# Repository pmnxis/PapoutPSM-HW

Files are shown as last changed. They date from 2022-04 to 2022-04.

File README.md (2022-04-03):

# PapoutPSM-HW

| 3D Model | Real Image |
| --- | --- |
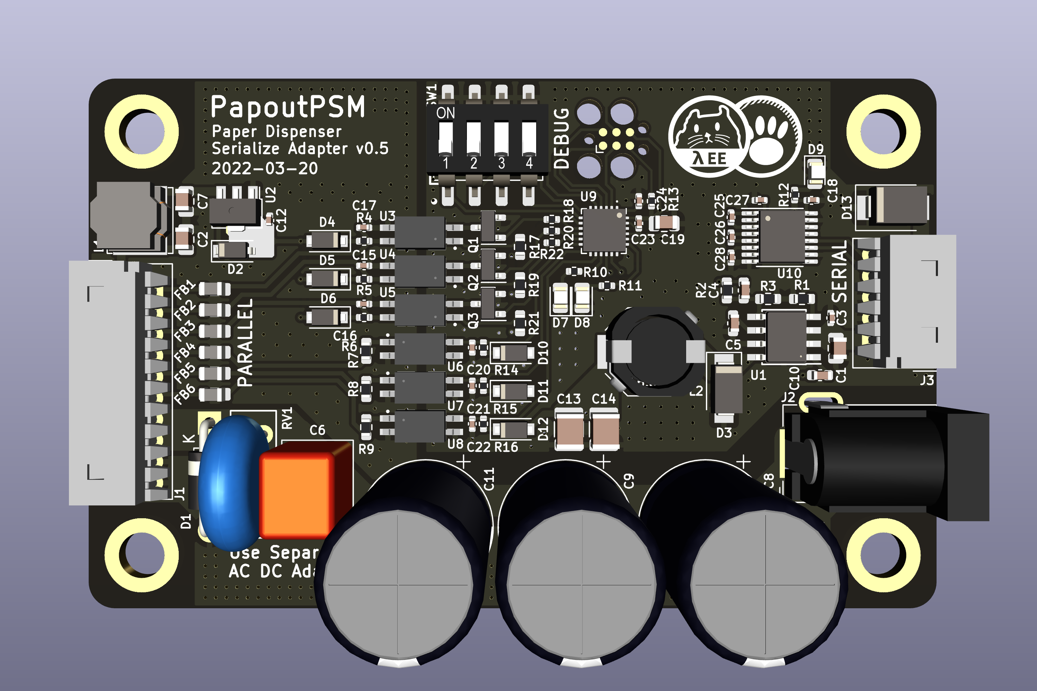
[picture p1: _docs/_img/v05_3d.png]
PCB 3D MODEL
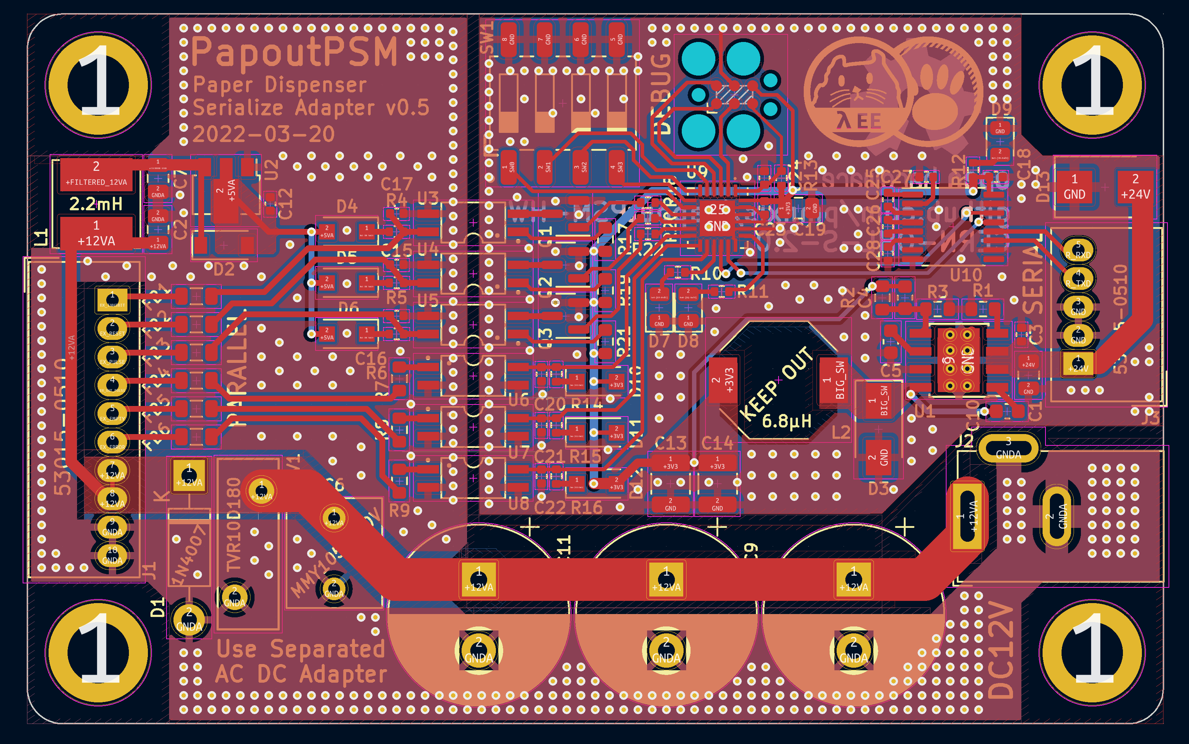
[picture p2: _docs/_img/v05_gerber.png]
GerberImage
|  |  |

Parallel to Serial Adapter for Korean Paper Dispenser Machine.
Some wellknown korean paper dispenser have two type of device.
Serial model communicate to host with RS232.

## PCB Specification
- DRC/Fabrication Clearance : JLCPCB Standard 2 Layer Spec.
- PCB : 2Layer FR4 ; 1.6T , Considerd on black colour.
- Size : 80mm * 50mm

## Power Connection
### 12V Usage (Normal)
- Connect Secondary Power Source (ACDC Adapter) 12VDC (5A) to barral jack.
- Use default varistor (RV1). Default is `10Ø 18V`.

### 24V Usage
- Connect Secondary Power Source (ACDC Adapter) 24VDC (3A) to barral jack.
- Use custom varistor (RV1). Must be higher or eqeual with `30V`.

### Programming
- MSP430FR2433 with CCStudio.
- or with Rust? https://github.com/rust-embedded/msp430-quickstart
- Emulating dispenser machine should count exhaust or some configuration on non violent storage. MSP43FR have internal FeRAM. Thus ensure high durability on many write operation.

### Related Project 
https://github.com/pmnxis/papout-psm-rs

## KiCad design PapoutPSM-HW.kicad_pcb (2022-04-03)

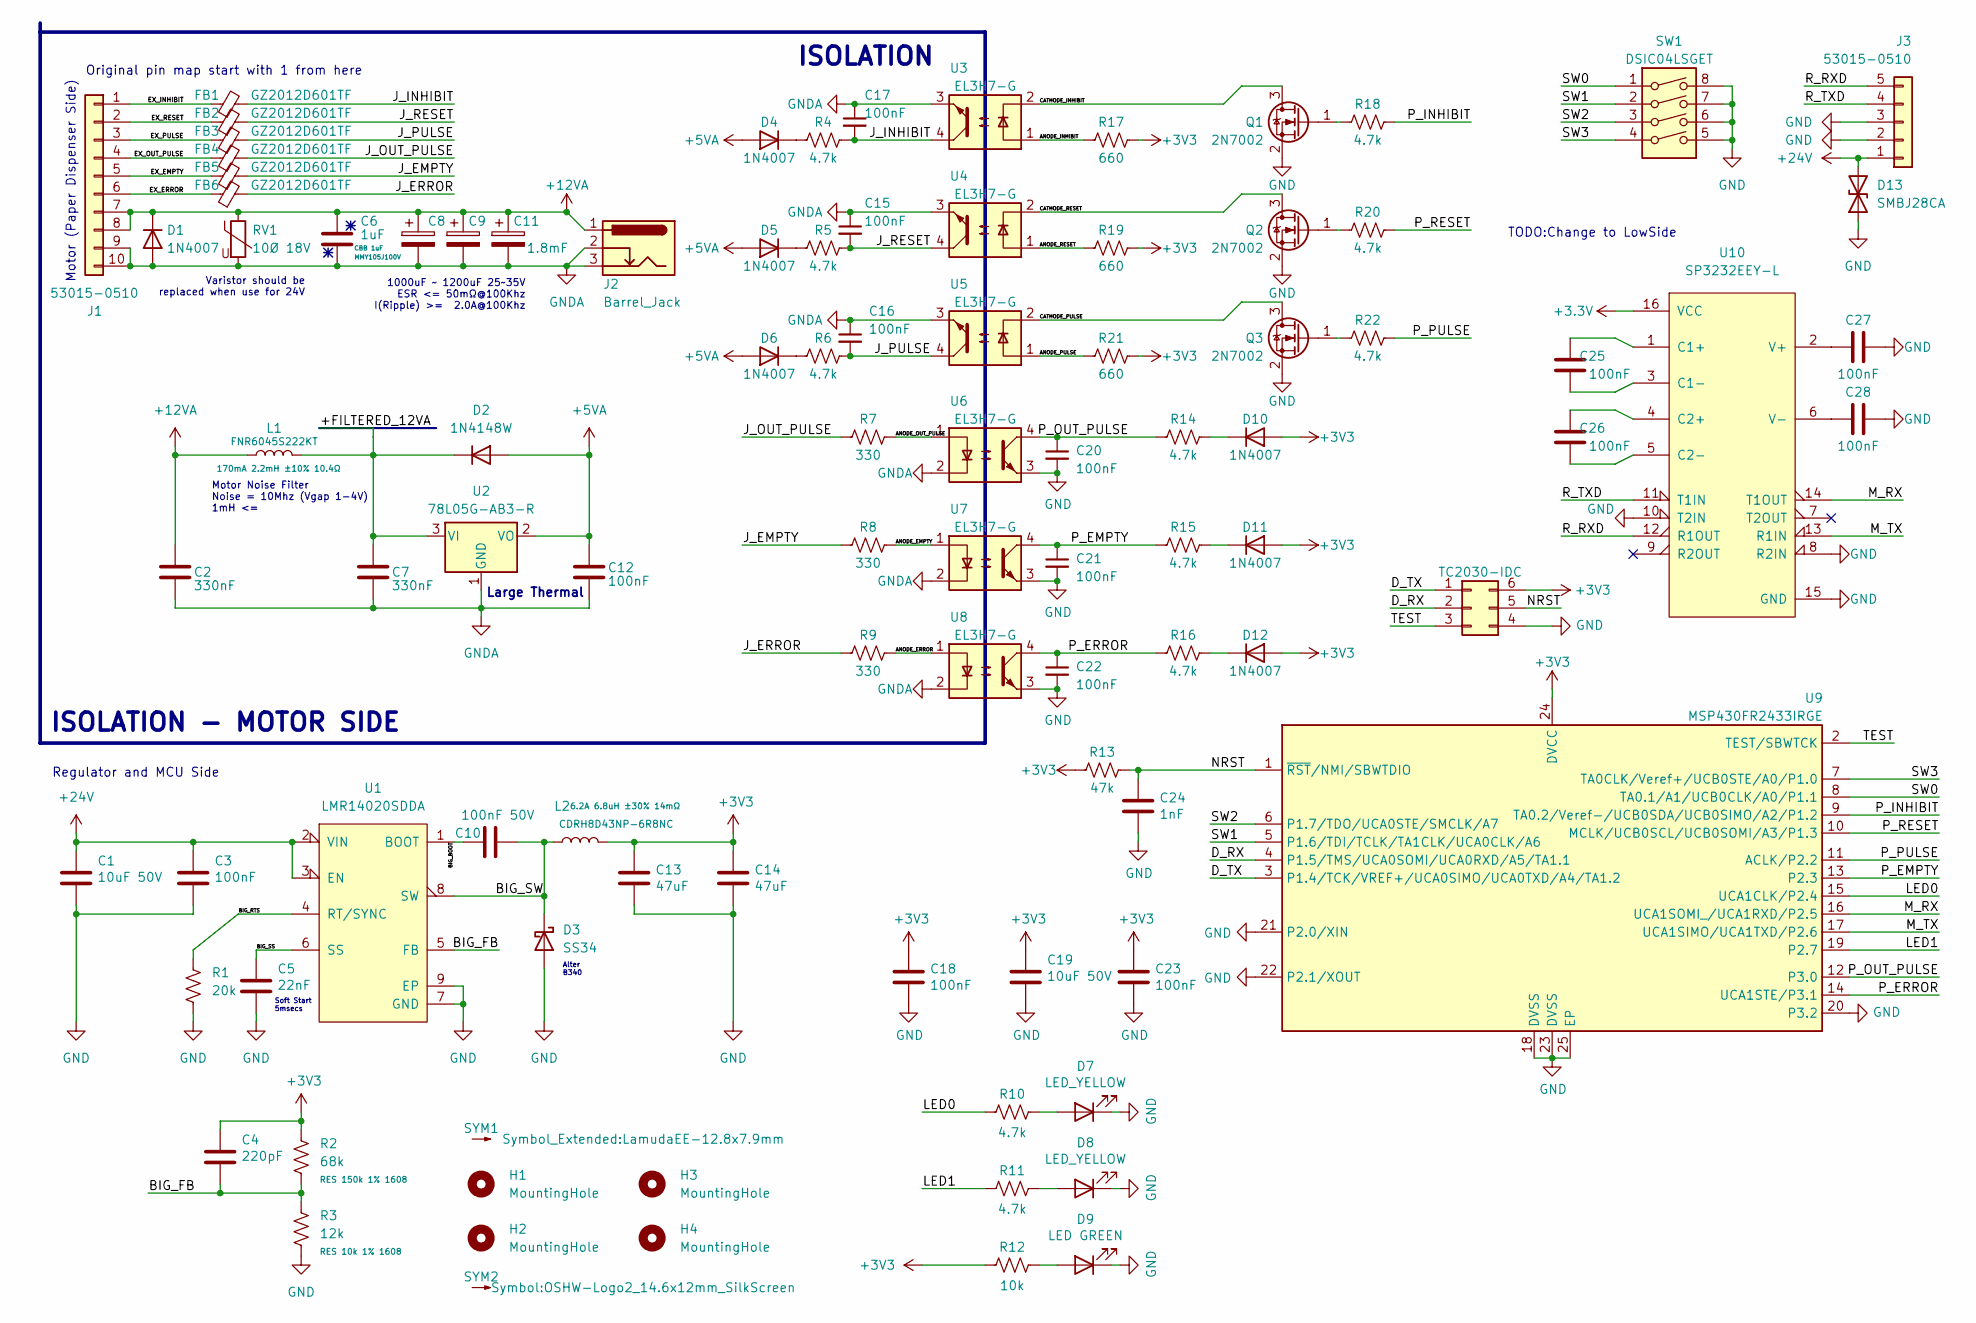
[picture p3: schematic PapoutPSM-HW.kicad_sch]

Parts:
C1, C19: 10uF 50V; C_0805_2012Metric; MFR.Part# GRM21BR61H106KE43L; LCSC Part C440198
C2, C7: 330nF; C_0805_2012Metric; MFR.Part# 0805B334K500NT; LCSC Part C1740
C3, C12, C15, C16, C17, C18, C20, C21, C22, C23, C25, C26, C27, C28: 100nF; C_0402_1005Metric; MFR.Part# CL05B104KB54PNC; LCSC Part C307331
C4: 220pF; C_0603_1608Metric; MFR.Part# CL10C331JB8NNNC; LCSC Part C1664
C5: 22nF; C_0603_1608Metric; MFR.Part# CL10B223KB8NNNC; LCSC Part C21122
C6: 1uF; C_Rect_L7.5mm_W6.5mm_P5.00mm; MFR.Part# MMY105J100V
C8, C9, C11: 1.8mF; CP_Radial_D12.5mm_P5.00mm; MFR.Part# LKML2501V182MF; LCSC Part C442894
C10: 100nF 50V; C_0603_1608Metric; MFR.Part# CC0603KRX7R9BB104; LCSC Part C14663
C13, C14: 47uF; C_1210_3225Metric; MFR.Part# GRM32ER61C476KE15L; LCSC Part C77101
C24: 1nF; C_0402_1005Metric; MFR.Part# 0402B102K500NT; LCSC Part C1523
D1: 1N4007; D_DO-41_SOD81_P10.16mm_Horizontal
D2: 1N4148W; D_SOD-123
D3: SS34; D_SMA; MFR.Part# SS34; LCSC Part C8678
D4, D5, D6, D10, D11, D12: 1N4007; D_SOD-123F
D7, D8: LED_YELLOW; LED_0805_2012Metric; MFR.Part# KT-0805Y; LCSC Part C2296
D9: LED GREEN; LED_0805_2012Metric; MFR.Part# KT-0805G; LCSC Part C2297
D13: SMBJ28CA; D_SMB; MFR.Part# SMBJ28CA; LCSC Part C151259
DEBUG1: TC2030-IDC; Tag-Connect_TC2030-IDC-FP_2x03_P1.27mm_Vertical
FB1, FB2, FB3, FB4, FB5, FB6: GZ2012D601TF; L_0805_2012Metric; MFR.Part# GZ2012D601TF; LCSC Part C1017
H1, H2, H3, H4: MountingHole; MountingHole_4.3mm_M4_ISO14580_Pad
J1: 53015-0510; Molex_MicroBlade_53015-1000_1x10_P2.00mm_Right; MFR.Part# 53015-1010
J2: Barrel_Jack; BarrelJack_GCT_DCJ200-10-A_Horizontal
J3: 53015-0510; Molex_MicroBlade_53015-0500_1x05_P2.00mm_Right; MFR.Part# 53015-0510
L1: FNR6045S222KT; L_Bourns_SRN6045TA; MFR.Part# FNR6045S222KT; LCSC Part C168104
L2: CDRH8D43NP-6R8NC; L_Bourns-SRU8028_8.0x8.0mm; MFR.Part# CDRH8D43NP-6R8NC; LCSC Part C225026
Q1, Q2, Q3: 2N7002; SOT-23
R1: 20k; R_0603_1608Metric; MFR.Part# 0603WAF2002T5E; LCSC Part C4184
R2: 68k; R_0603_1608Metric; MFR.Part# 0603WAF1503T5E; LCSC Part C22807
R3: 12k; R_0603_1608Metric; MFR.Part# 0603WAF1002T5E; LCSC Part C25804
R4, R5, R6, R10, R11, R14, R15, R16, R18, R20, R22: 4.7k; R_0402_1005Metric; MFR.Part# 0402WGF4701TCE; LCSC Part C25900
R7, R8, R9: 330; R_0603_1608Metric
R12: 10k; R_0402_1005Metric; MFR.Part# 0402WGF1002TCE; LCSC Part C25744
R13: 47k; R_0402_1005Metric; MFR.Part# 0402WGF4702TCE; LCSC Part C25792
R17, R19, R21: 660; R_0603_1608Metric
RV1: 10Ø 18V; RV_Disc_D12mm_W4.3mm_P7.5mm
SW1: DSIC04LSGET; SW_DIP_SPSTx04_Slide_9.30x10.16mm_W4.25mm_P2.54mm
SYM1: SYM_Arrow_Tiny; LamudaEE-12.8x7.9mm
SYM2: SYM_Arrow_Tiny; OSHW-Logo2_14.6x12mm_SilkScreen
U1: LMR14020SDDA; TI_SO-PowerPAD-8_ThermalVias; MFR.Part# LMR14050SDDAR; LCSC Part C155484
U2: 78L05G-AB3-R; SOT-89-3; MFR.Part# 78L05G-AB3-R; LCSC Part C71136
U3, U4, U5, U6, U7, U8: EL3H7-G; SMDIP-4_W5.20mm; MFR.Part# EL3H7(B)(TA)-G; LCSC Part C32565
U9: MSP430FR2433IRGE; HVQFN-24-1EP_4x4mm_P0.5mm_EP2.5x2.5mm; MFR.Part# MSP430FR2433IRGER; LCSC Part C191026
U10: SP3232EEY-L; TSSOP-16_4.4x5mm_P0.65mm; MFR.Part# SP3232EEY-L; LCSC Part C13482

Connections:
+5VA: C12.1, D2.2 (A), D4.2 (A), D5.2 (A), D6.2 (A), U2.2 (VO)
+12VA: C2.1, C6.1, C8.1, C9.1, C11.1, D1.1 (K), J1.7, J1.8, J2.1, L1.1, RV1.1
+24V: C1.1, C3.1, D13.2 (A2), J3.1, U1.2 (VIN), U1.3 (EN)
/+FILTERED_12VA: C7.1, D2.1 (K), L1.2, U2.3 (VI)
/ANODE_EMPTY: R8.2, U7.1
/ANODE_ERROR: R9.2, U8.1
/ANODE_INHIBIT: R17.1, U3.1
/ANODE_OUT_PULSE: R7.2, U6.1
/ANODE_PULSE: R21.1, U5.1
/ANODE_RESET: R19.1, U4.1
/BIG_BOOT: C10.1, U1.1 (BOOT)
/BIG_FB: C4.2, R2.2, R3.1, U1.5 (FB)
/BIG_RTS: R1.1, U1.4 (RT/SYNC)
/BIG_SS: C5.1, U1.6 (SS)
/BIG_SW: C10.2, D3.1 (K), L2.1, U1.8 (SW)
/CATHODE_INHIBIT: Q1.3 (D), U3.2
/CATHODE_PULSE: Q3.3 (D), U5.2
/CATHODE_RESET: Q2.3 (D), U4.2
/D_RX: DEBUG1.2, U9.4 (P1.5/TMS/UCA0SOMI/UCA0RXD/A5/TA1.1)
/D_TX: DEBUG1.1, U9.3 (P1.4/TCK/VREF+/UCA0SIMO/UCA0TXD/A4/TA1.2)
/EX_EMPTY: FB5.1, J1.5
/EX_ERROR: FB6.1, J1.6
/EX_INHIBIT: FB1.1, J1.1
/EX_OUT_PULSE: FB4.1, J1.4
/EX_PULSE: FB3.1, J1.3
/EX_RESET: FB2.1, J1.2
/J_EMPTY: FB5.2, R8.1
/J_ERROR: FB6.2, R9.1
/J_INHIBIT: C17.2, FB1.2, R4.2, U3.4
/J_OUT_PULSE: FB4.2, R7.1
/J_PULSE: C16.2, FB3.2, R6.2, U5.4
/J_RESET: C15.2, FB2.2, R5.2, U4.4
/LED0: R10.1, U9.15 (UCA1CLK/P2.4)
/LED1: R11.1, U9.19 (P2.7)
/M_RX: U9.16 (UCA1SOMI_/UCA1RXD/P2.5), U10.14 (T1OUT)
/M_TX: U9.17 (UCA1SIMO/UCA1TXD/P2.6), U10.13 (R1IN)
/NRST: C24.1, DEBUG1.5, R13.1, U9.1 (~RST/NMI/SBWTDIO)
/P_EMPTY: C21.1, R15.2, U7.4, U9.13 (P2.3)
/P_ERROR: C22.1, R16.2, U8.4, U9.14 (UCA1STE/P3.1)
/P_INHIBIT: R18.2, U9.9 (TA0.2/Veref-/UCB0SDA/UCB0SIMO/A2/P1.2)
/P_OUT_PULSE: C20.1, R14.2, U6.4, U9.12 (P3.0)
/P_PULSE: R22.2, U9.11 (ACLK/P2.2)
/P_RESET: R20.2, U9.10 (MCLK/UCB0SCL/UCB0SOMI/A3/P1.3)
/R_RXD: J3.5, U10.12 (R1OUT)
/R_TXD: J3.4, U10.11 (T1IN)
/SW0: SW1.1, U9.8 (TA0.1/A1/UCB0CLK/A0/P1.1)
/SW1: SW1.2, U9.5 (P1.6/TDI/TCLK/TA1CLK/UCA0CLK/A6)
/SW2: SW1.3, U9.6 (P1.7/TDO/UCA0STE/SMCLK/A7)
/SW3: SW1.4, U9.7 (TA0CLK/Veref+/UCB0STE/A0/P1.0)
/TEST: DEBUG1.3, U9.2 (TEST/SBWTCK)
GND: C1.2, C3.2, C5.2, C13.2, C14.2, C18.2, C19.2, C20.2, C21.2, C22.2, C23.2, C24.2, C27.1, C28.1, D3.2 (A), D7.1 (K), D8.1 (K), D9.1 (K), D13.1 (A1), DEBUG1.4, J3.2, J3.3, Q1.2 (S), Q2.2 (S), Q3.2 (S), R1.2, R3.2, SW1.5, SW1.6, SW1.7, SW1.8, U1.7 (GND), U1.9 (EP), U6.3, U7.3, U8.3, U9.18 (DVSS), U9.20 (P3.2), U9.21 (P2.0/XIN), U9.22 (P2.1/XOUT), U9.23 (DVSS), U9.25 (EP), U10.8 (R2IN), U10.10 (T2IN), U10.15 (GND)
GNDA: C2.2, C6.2, C7.2, C8.2, C9.2, C11.2, C12.2, C15.1, C16.1, C17.1, D1.2 (A), J1.9, J1.10, J2.2, J2.3, RV1.2, U2.1 (GND), U3.3, U4.3, U5.3, U6.2, U7.2, U8.2
unnamed: C25.1, U10.3 (C1-)
unnamed: C25.2, U10.1 (C1+)
unnamed: C26.1, U10.5 (C2-)
unnamed: C26.2, U10.4 (C2+)
unnamed: C27.2, U10.2 (V+)
unnamed: C28.2, U10.6 (V-)
unnamed: D4.1 (K), R4.1
unnamed: D5.1 (K), R5.1
unnamed: D6.1 (K), R6.1
unnamed: D7.2 (A), R10.2
unnamed: D8.2 (A), R11.2
unnamed: D9.2 (A), R12.2
unnamed: D10.1 (K), R14.1
unnamed: D11.1 (K), R15.1
unnamed: D12.1 (K), R16.1
unnamed: Q1.1 (G), R18.1
unnamed: Q2.1 (G), R20.1
unnamed: Q3.1 (G), R22.1

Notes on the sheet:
Alter B340
Soft Start 5msecs
Regulator and MCU Side
1000uF ~ 1200uF 25~35V ESR <= 50mΩ@100Khz I(Ripple) >= 2.0A@100Khz
ISOLATION
TODO:Change to LowSide
Motor Noise Filter Noise = 10Mhz (Vgap 1-4V) 1mH <=
Large Thermal
ISOLATION - MOTOR SIDE
Original pin map start with 1 from here
Varistor should be replaced when use for 24V
Motor (Paper Dispenser Side)

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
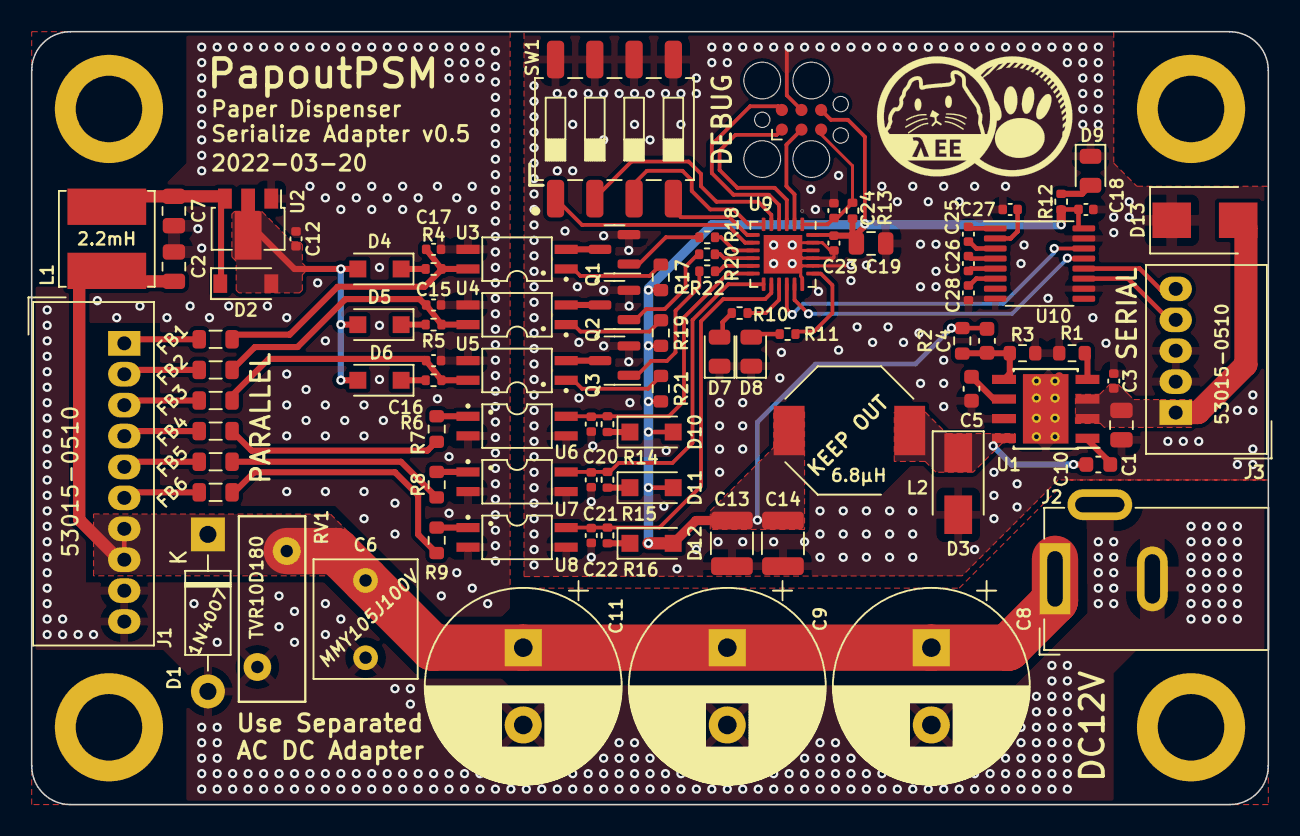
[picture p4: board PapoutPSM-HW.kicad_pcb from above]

Board: 2 copper layers, 80.0 x 50.0 mm, 96 parts (1 on the bottom side), 71 nets.

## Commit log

2021-07-28 update bom
    [PapoutPSM-HW.kicad_pcb, PapoutPSM-HW.kicad_sch, Parallel_IO.kicad_sch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]
2021-07-28 update bom2
    [PapoutPSM-HW.kicad_sch, Parallel_IO.kicad_sch, Power.kicad_sch]
2021-07-29 updates pdf.
    [PapoutPSM-HW.kicad_sch, Parallel_IO.kicad_sch, Power.kicad_sch]
2021-07-31 pre 2
    [PapoutPSM-HW.kicad_pcb, PapoutPSM-HW.kicad_sch, Parallel_IO.kicad_sch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]
2022-01-31 released kicad 6.0
2022-03-20 release/v3 update
    [PapoutPSM-HW.kicad_pcb, PapoutPSM-HW.kicad_sch, Parallel_IO.kicad_sch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]
2022-03-20 before release v0.5
    [PapoutPSM-HW.kicad_pcb, PapoutPSM-HW.kicad_sch, Parallel_IO.kicad_sch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]
2022-04-03 Update latest changes on low-side NMos usage
    [PapoutPSM-HW.kicad_pcb, PapoutPSM-HW.kicad_sch]

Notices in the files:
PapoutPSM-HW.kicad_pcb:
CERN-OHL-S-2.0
